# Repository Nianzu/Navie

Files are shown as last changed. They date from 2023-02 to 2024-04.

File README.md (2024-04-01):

# Navie

A little robot that navigates entirely on its own. Hence the name, Navie.

## Implemented Features
* Onboard navigation processing
* Onboard vision processing

## Desired Features
* Extremely low upfront cost (<$100)
* Stereo camera for navigation
* Use brushless motors as drive system
    * FOC on brushless motors
    * Custom motor driver circuit
* Really small (Fit in the palm of the hand)
* Integrated rechargeable battery
* WIFI connectivity



## Technologies
### Depth processing
Depth processing is done using a block-matching algorithm where each pixel is calculated individually, and neighbors are only processed for sub-pixel calculations. In the future, I plan to implement pyramiding and already have the Gaussian resizing function completed.

### Localization
Localization is currently a simple particle filter, with Gaussian noise generated by this function. Currently, there is no past knowledge within each particle, but there are plans to update this in the future.

The algorithm outputs a "best guess" position on the map that the path planner then uses to attempt to route the robot to the goal location.

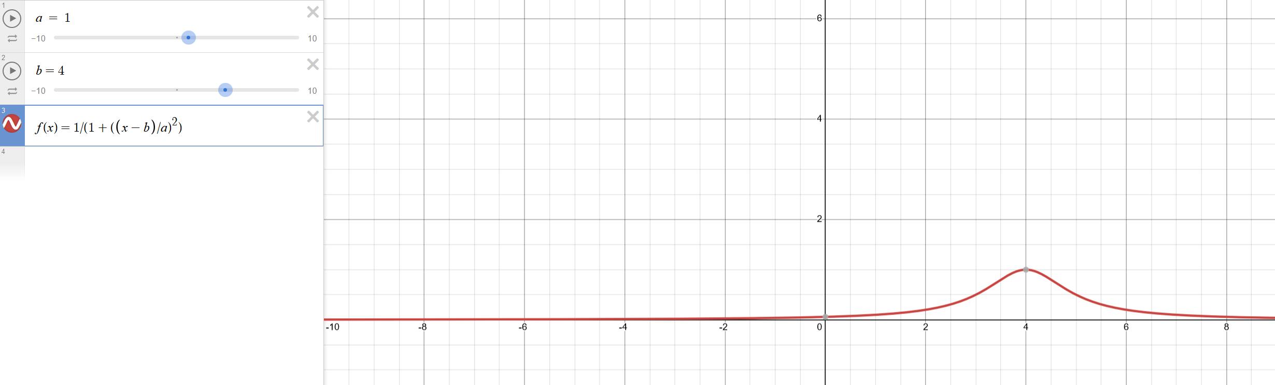
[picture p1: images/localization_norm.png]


### Path planning
The path planning implementation is designed to take a single path with x_1,y_1 start points and x_2,y_2 end points, and recursively split it using an A* approach to generate a valid path. Currently, the path-splitting is buggy so its been removed. Below is a demonstration of the localization and path planning working together to get a robot (white circle with red lines) to the goal position (end of white line) using only the knowledge of the length of the 3 sensors and the map.

You might notice that the green circle/line (the best guess robot) is not correct at first. This is because the map is highly symmetric, so there are lots of valid positions at first

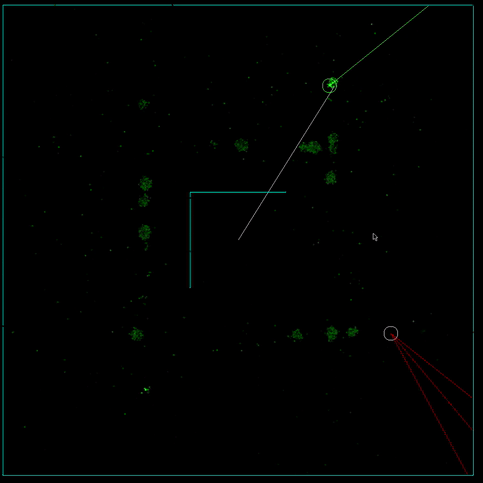
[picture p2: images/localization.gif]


## Hardware
### Processor - Raspberry Pi 4B AND  Raspberry Pi 3 B V1.2
Ideally, this will eventually be a fully custom processor. However, I've been able to benchmark the processing on a Raspberry Pi 4B and it looks like this will be able to run under a second for a full cycle **without any additional optimizations**. Seeing as 1 second was my initial target when I started this project, this is good enough for now. However, due to my choice of camera, I'll have to run 2 pies. The cameras plug into the pi's camera port, and I don't want to pay for a camera multiplexer. So, the plan is for the Pi 4 to transfer the image to the Pi 3, which will run the depth processing. Then the Pi 3 will output sensor vectors to the Pi 4 which will run the particle filter and the motors.

### Cameras - OV5647 x2
Why these cameras? 1: They are cheap. I managed to find a set of 2 of these on amazon for $9. 2: They are high performing, promising 2592 x 1944 still images, 1080p video, and up to 90 fps at 640x480. TODO What more do I need?

<image src="images/OV5647.jpg" width=200>

[Arducam link](https://www.arducam.com/product/arducam-ov5647-standard-raspberry-pi-camera-b0033/)

[Amazon link](https://www.amazon.com/gp/product/B07ZZ2K7WP/ref=ox_sc_act_title_3?smid=A20BQYJRA135IQ&psc=1)

### Motors - N20 knockoff
What do I need in a motor? Encoder feedback, decent build quality, low size and weight. I wanted to get [these](https://www.servocity.com/90-rpm-micro-gear-motor-w-encoder/) from servo city, but I found what looks to be a knockoff on Amazon for half the price. TODO We'll see if I get what I paid for.

<image src="images/motor.jpg" width=200>

[Amazon link](https://www.amazon.com/Reduction-Multiple-Replacement-Velocity-Measurement/dp/B08DKJT2XF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)

### Motor controler - L298N
Cheap, reliable, and most importantly cheap.

<image src="images/motor_driver.jpg" width=200>

[Amazon link](https://www.amazon.com/HiLetgo-Controller-Stepper-H-Bridge-Mega2560/dp/B07BK1QL5T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)

### Power converter - LM2596
### Integration and cooling

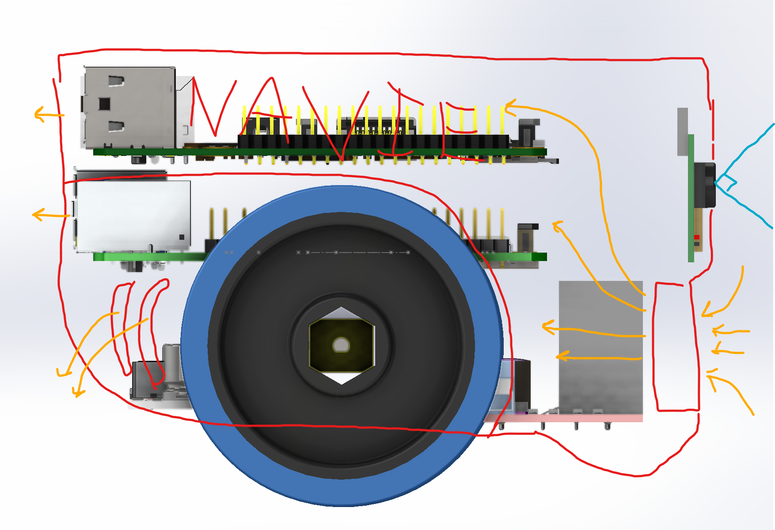
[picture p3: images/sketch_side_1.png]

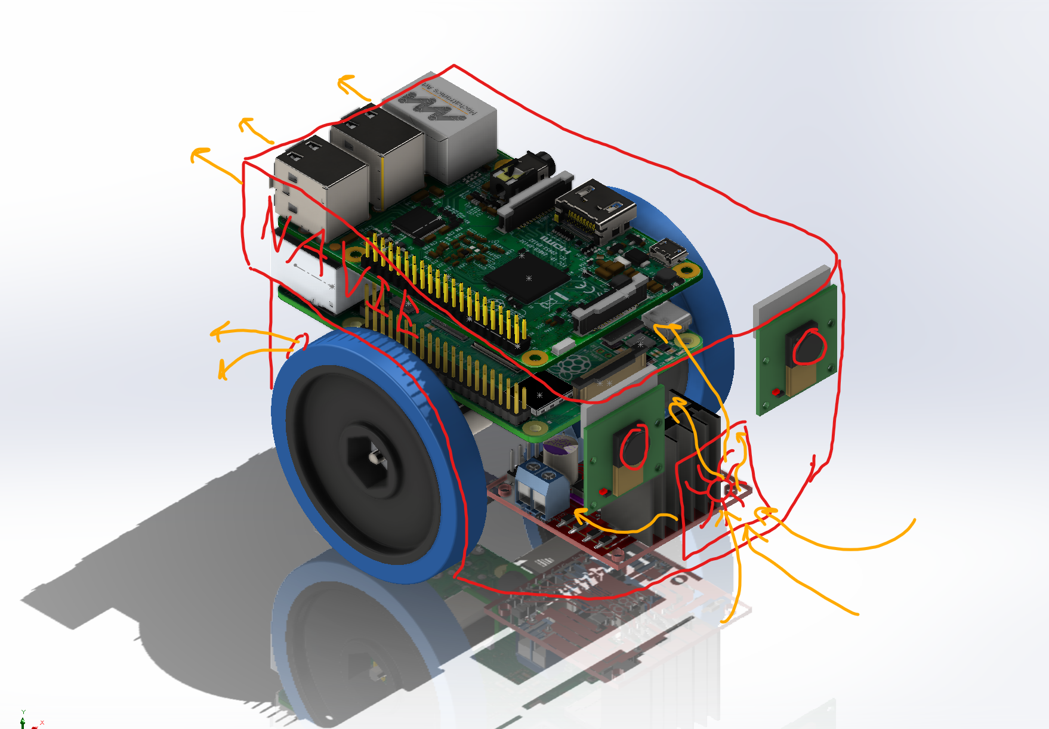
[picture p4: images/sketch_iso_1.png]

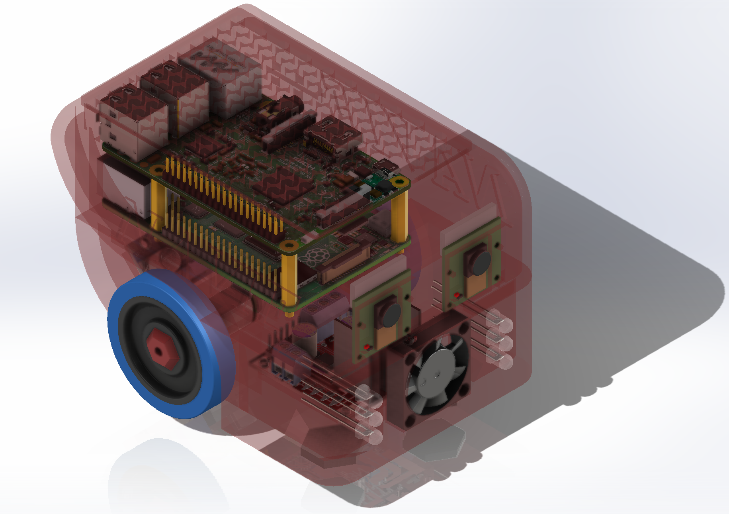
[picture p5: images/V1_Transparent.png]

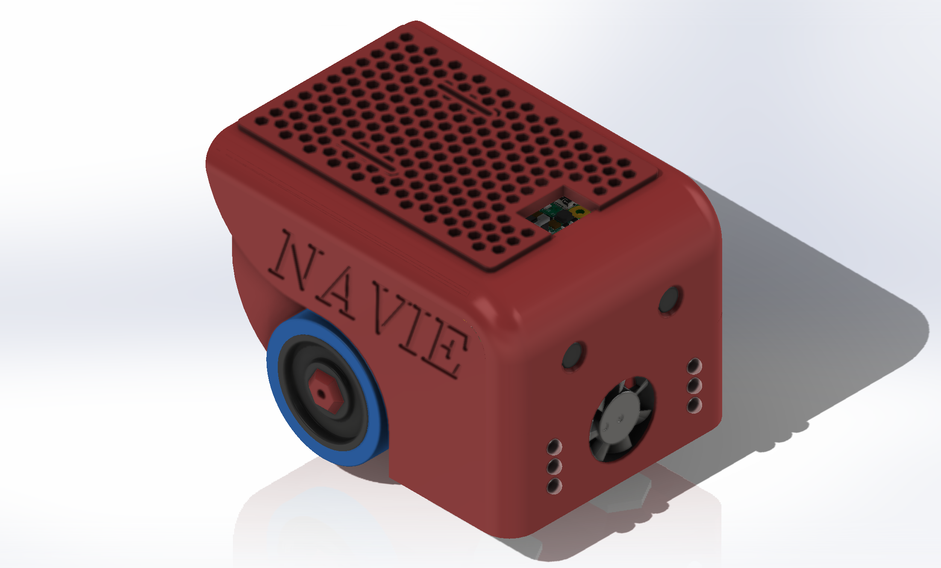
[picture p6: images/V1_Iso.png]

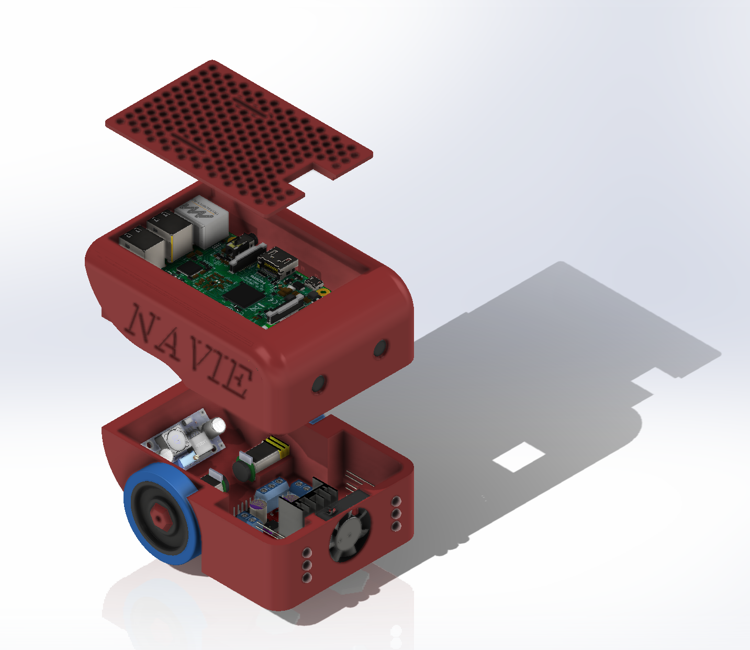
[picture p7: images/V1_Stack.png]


https://banebots.com/banebots-wheel-2-3-8-x-0-4-1-2-hex-mount-50a-black-blue/

## Getting Started
TODO write this section

### Dev environment setup
* Ubuntu running under WSL with VcXsrv for test processes, 
* Non-STL libraries
    * Simple Direct Media Layer (SDL 2) `<SDL2/SDL.h>`. Used to write pixels to the screen. Used due to strong support, ease of use, and cross-platform support.
    ```
    sudo apt install libsdl2-dev
    ```
    * NCurses  `<ncurses.h>`. Used to get key inputs from the user to drive the robot in manual mode.
    ```
    sudo apt install libncurses5-dev libncursesw5-dev
    ```
    * Terminos  `<termios.h>`. Used to set the terminal to non-cannonical mode for easier driving. Seems to come pre-installed with linux, TODO need to check.
    * bcm2835 `<bcm2835.h>`. Used to control the bcm2835 chip on the raspberry pi that handles GPIO. This is our GPIO library.
    ```
    wget http://www.airspayce.com/mikem/bcm2835/bcm2835-1.71.tar.gz
    tar zxvf bcm2835-1.71.tar.gz
    cd bcm2835-1.71
    ./configure
    make
    sudo make check
    sudo make install
    ```

### Compile

#### Depth processing
```
gcc -g main.c -o main.o
```

#### Localization (All subprograms)
```
gcc main.c -o main.o `sdl2-config --cflags --libs` -lm -O3
```

#### Control
```
gcc -o main main.c -lm -lbcm2835
```

#### Test
```
gcc main.c -o main.o
```

## To-Do

### Depth processing
* Confidence rejection
* Filter output image
* Rectify images (not using Middlebury dataset)

### Localization
* Particle filter often finds the wrong node cluster at first.
* Particle filter does not take into account recent history.
* Path planner
* Flood on loss of confidence

### Mechanical
* Consider installing a laser pointer to aid in depth perception of featureless walls. (structured light)
* move zipties back
* Motor driver needs to be filed for fit (too tight)
* Motor driver aleged ineficiencies
* motor driver size
* Wheel hub D shaft is not tight enough. Radius is good, increase length of D-line
* Camera cad is incorrect

## Benchmarks - Depth processing

Execution time for `depth_processing\tsukuba\scene1.row3.col1.ppm` and `depth_processing\tsukuba\scene1.row3.col2.ppm`. All performance is single threaded to make comparisons to future hardware more apt.

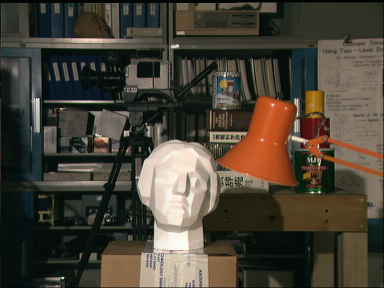
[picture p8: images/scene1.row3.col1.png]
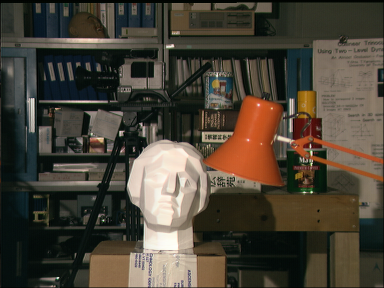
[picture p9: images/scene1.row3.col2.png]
 

### 2/16/2022 Simple block match

```
287/288 - 100%
block_match() took 90.131191 seconds to execute
```
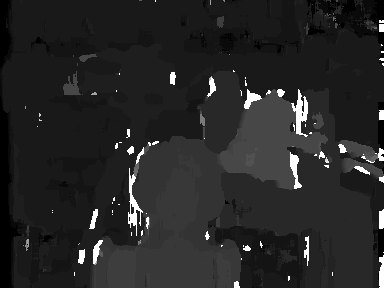
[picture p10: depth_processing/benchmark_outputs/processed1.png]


### 2/17/2022 Full-color block match

```
287/288 - 100%
block_match() took 87.297683 seconds to execute
```
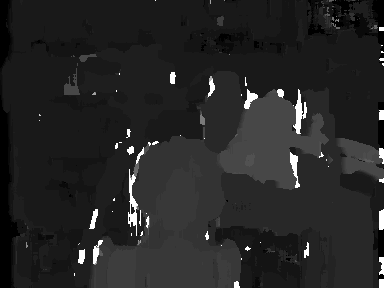
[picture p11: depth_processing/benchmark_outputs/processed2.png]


### 2/17/2022 Fixed block-matching length issue

```
287/288 - 100%
block_match() took 21.699990 seconds to execute
```
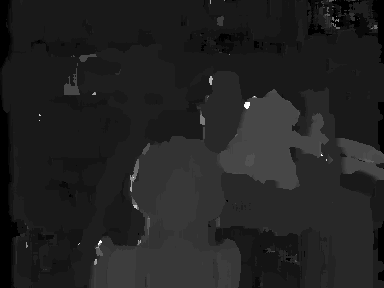
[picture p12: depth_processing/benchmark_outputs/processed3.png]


### 2/17/2022 Sup-pixel disparity

```
287/288 - 100%
block_match() took 21.609720 seconds to execute
```
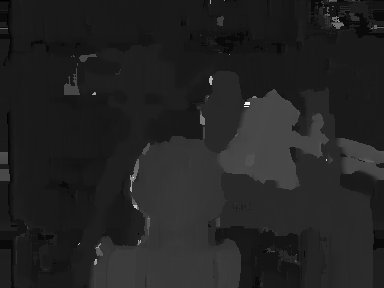
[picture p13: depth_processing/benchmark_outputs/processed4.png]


### 2/17/2022 Search-box optimization + better data structure for depth map

```
287/288 - 100%
block_match() took 3.112148 seconds to execute
```
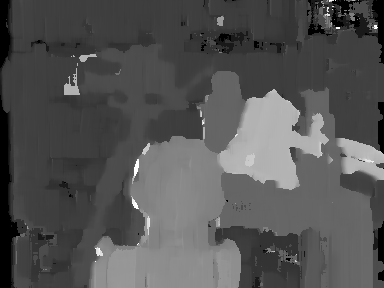
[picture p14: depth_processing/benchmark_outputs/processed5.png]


block_match() took 0.682072 seconds to execute

### 2/20/2022 Added -O3 compiler flag and removed unnecessary prints

```
block_match() took 0.682072 seconds to execute
```


## Benchmarks - Localization

### 2/20/2022 Simple particle filter
T-0
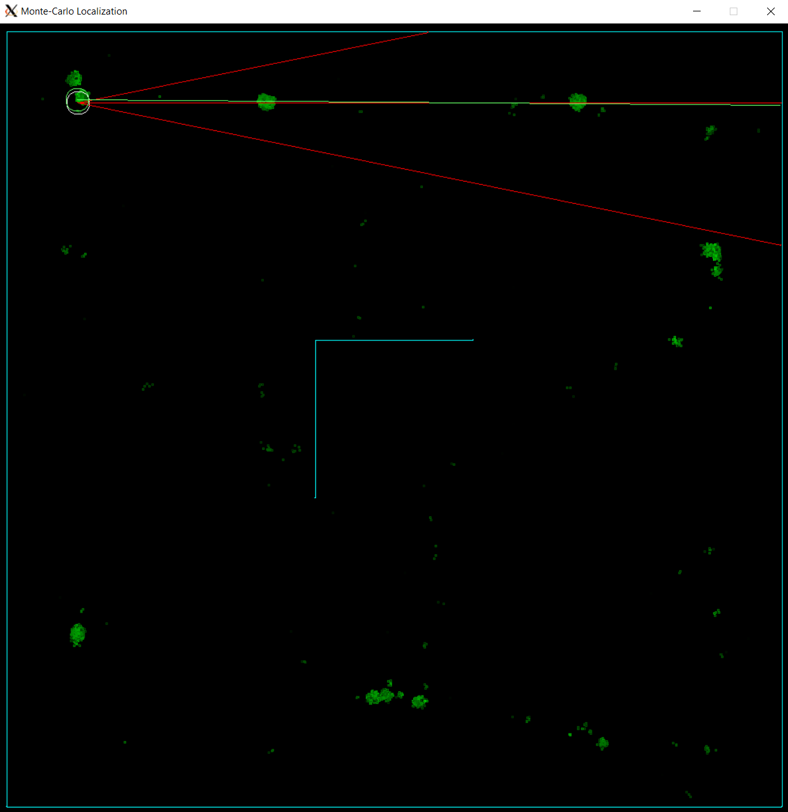
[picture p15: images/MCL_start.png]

T-1
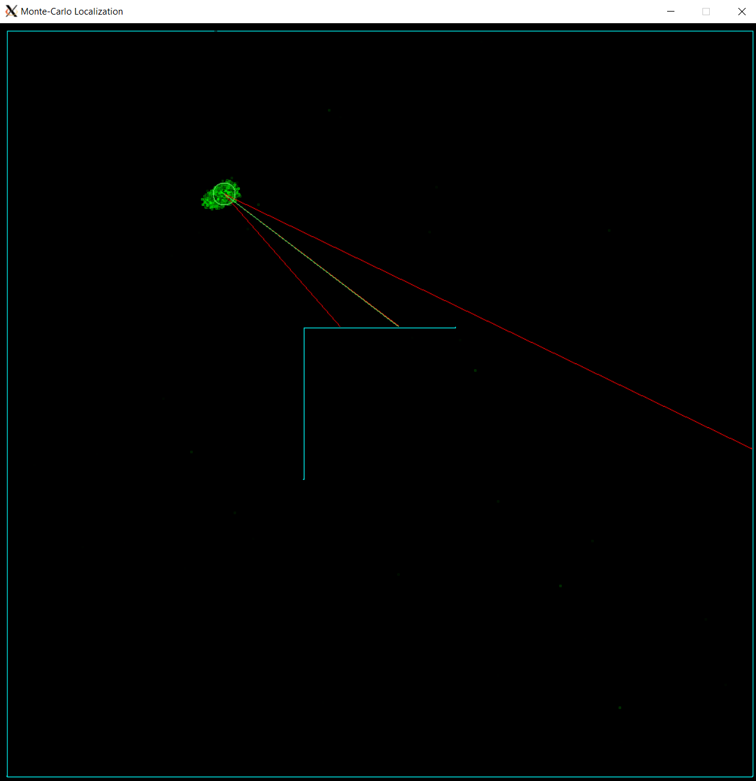
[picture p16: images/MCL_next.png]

```
processing (not including graphics) took 0.027040 seconds to execute.
```
Execution time is ~0.015s per frame, including path planning and particle filtering with 5000 particles.

## Hardware benchmarks

### Raspberry Pi 3 B V1.2
#### Localization
Software Version: 2d94655dcabb89866f78500f899f6fc5ea158938
```
processing (not including graphics) took 0.522824 seconds to execute
```

### Raspberry Pi 4 B
#### Localization
Software Version: 2d94655dcabb89866f78500f899f6fc5ea158938
```
processing (not including graphics) took 0.190935 seconds to execute
```

## Sources
These are the sources that I used to inform my decision on this project, and that I think might be helpful to someone attempting something similar. I've made an effort to provide a general explanation of each source.

### Depth processing
* *Stereo Vision: Depth Estimation between object and camera* - Apar Garg 
    * Generalist beginner explanation of depth processing using block matching, and some of the math behind determining the depth of each pixel.
    * Includes some source code in python
    * https://medium.com/analytics-vidhya/distance-estimation-cf2f2fd709d8

* *Middlebury Stereo Datasets*
    * Great resource for image pairs to test depth processing. Ground truth images are sometimes included.
    * https://vision.middlebury.edu/stereo/data/

* *Depth Estimation: Basics and Intuition* - Daryl Tan
    * Overview of the state of depth processing in CS, including stereo and monocular techniques.
    * Great for understanding the options available for depth processing.
    * https://towardsdatascience.com/depth-estimation-1-basics-and-intuition-86f2c9538cd1

Background (Research paper): https://citeseerx.ist.psu.edu/document?repid=rep1&type=pdf&doi=32aedb3d4e52b879de9a7f28ee0ecee997003271

Background: https://ww2.mathworks.cn/help/visionhdl/ug/stereoscopic-disparity.html

TODO + Source: https://docs.opencv.org/3.4/d3/d14/tutorial_ximgproc_disparity_filtering.html

Dataset: http://sintel.is.tue.mpg.de/depth

Background: https://www.cs.cmu.edu/~16385/s17/Slides/13.2_Stereo_Matching.pdf

Background: http://mccormickml.com/2014/01/10/stereo-vision-tutorial-part-i/

TODO: https://developer.nvidia.com/how-to-cuda-c-cpp

Background: https://dsp.stackexchange.com/questions/75899/appropriate-gaussian-filter-parameters-when-resizing-image

### Localization

Background (Research paper): https://www.ri.cmu.edu/pub_files/pub1/dellaert_frank_1999_2/dellaert_frank_1999_2.pdf

Background + Source: https://fjp.at/posts/localization/mcl/

Background + Source: https://ros-developer.com/2019/04/10/parcticle-filter-explained-with-python-code-from-scratch/

Background (REALLY GOOD): https://www.usna.edu/Users/cs/taylor/courses/si475/notes/slam.pdf

Example: https://www.youtube.com/watch?v=m3L8OfbTXH0

Background (REALLY GOOD):https://www.youtube.com/watch?v=3Yl2aq28LFQ

Background (Research paper): https://research.google.com/pubs/archive/45466.pdf

Background (REALLY GOOD): https://cs.gmu.edu/~kosecka/cs685/cs685-icp.pdf

Background (Research paper): https://arxiv.org/pdf/2007.07627

Background (Research paper): https://www.researchgate.net/figure/Hybrid-algorithm-ideology-ICP-step-by-step-comes-to-local-minima-After-local-minima_fig4_281412803

https://towardsdatascience.com/optimization-techniques-simulated-annealing-d6a4785a1de7
https://resources.mpi-inf.mpg.de/deformableShapeMatching/EG2011_Tutorial/slides/2.1%20Rigid%20ICP.pdf
https://www.visiondummy.com/2014/04/geometric-interpretation-covariance-matrix/
https://www.youtube.com/watch?v=cOUTpqlX-Xs
https://cs.fit.edu/~dmitra/SciComp/Resources/singular-value-decomposition-fast-track-tutorial.pdf
https://iosoft.blog/2020/07/16/raspberry-pi-smi/
https://forums.raspberrypi.com/viewtopic.php?t=228727
https://raspberrypi.stackexchange.com/questions/130529/how-fast-are-c-python-libraries
https://forums.raspberrypi.com/viewtopic.php?t=244031
PERIPHERAL BASE ADDRESS FOR RASPBERRY PI 4 is  0xFE000000
https://raspberrypi.stackexchange.com/questions/124985/using-motor-encoders-with-raspberry-pi
### Camera processing
Background: https://www.raspberrypi.com/documentation/computers/camera_software.html#getting-started

Source: https://stackoverflow.com/questions/41440245/reading-camera-image-using-raspistill-from-c-program

Server Stream: libcamera-vid -t 0 --inline --listen -o tcp://0.0.0.0:8000
Server Stream 60fps: libcamera-vid -t 0 --inline --listen -o tcp://0.0.0.0:8000 --level 4.2 --framerate 120 --width 1280 --height 720 --denoise cdn_off

Client: ffplay tcp://10.0.0.73:8000 -vf "setpts=N/30" -fflags nobuffer -flags low_delay -framedrop
ffplay tcp://10.0.0.73:8000 -vf "hflip,vflip" -flags low_delay -framedrop

## Contributions

Contributions are always welcome. If you want to contribute to the project, please create a pull request.

## License

This project is not currently licensed, but I will look into adding a license at a later date.

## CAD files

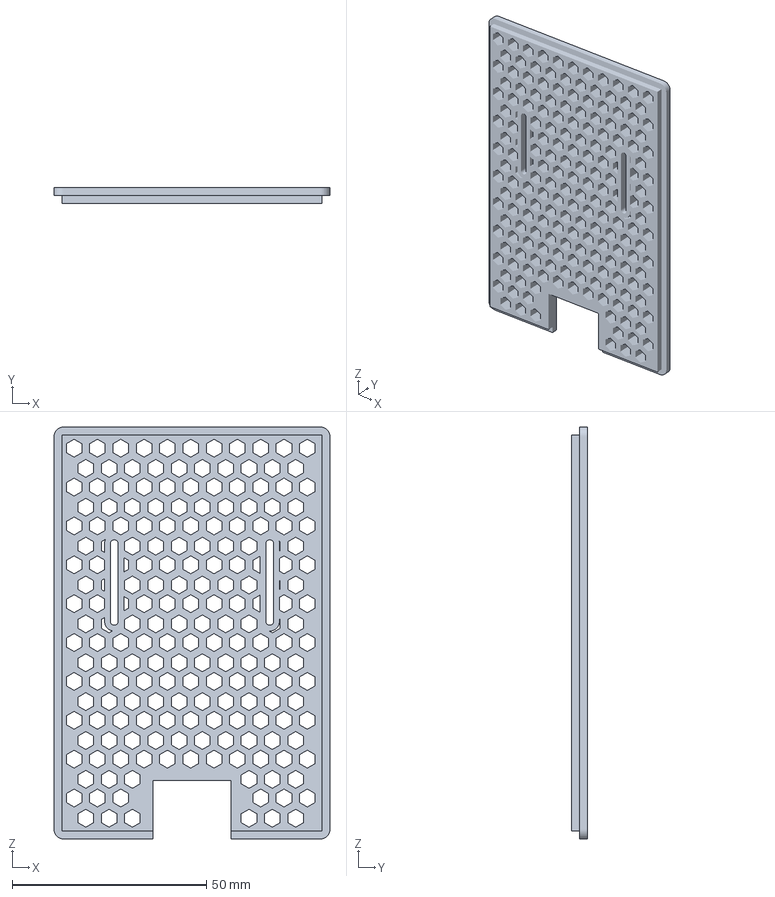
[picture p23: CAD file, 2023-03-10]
hardware/3D prints/lid.3MF
71.0 x 4.00 x 106.0 mm

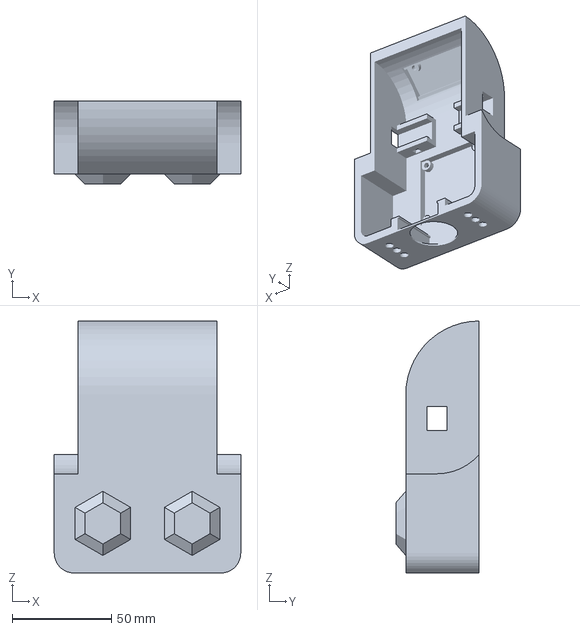
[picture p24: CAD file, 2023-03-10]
hardware/3D prints/base_frame.3MF
94.0 x 42.0 x 127.0 mm

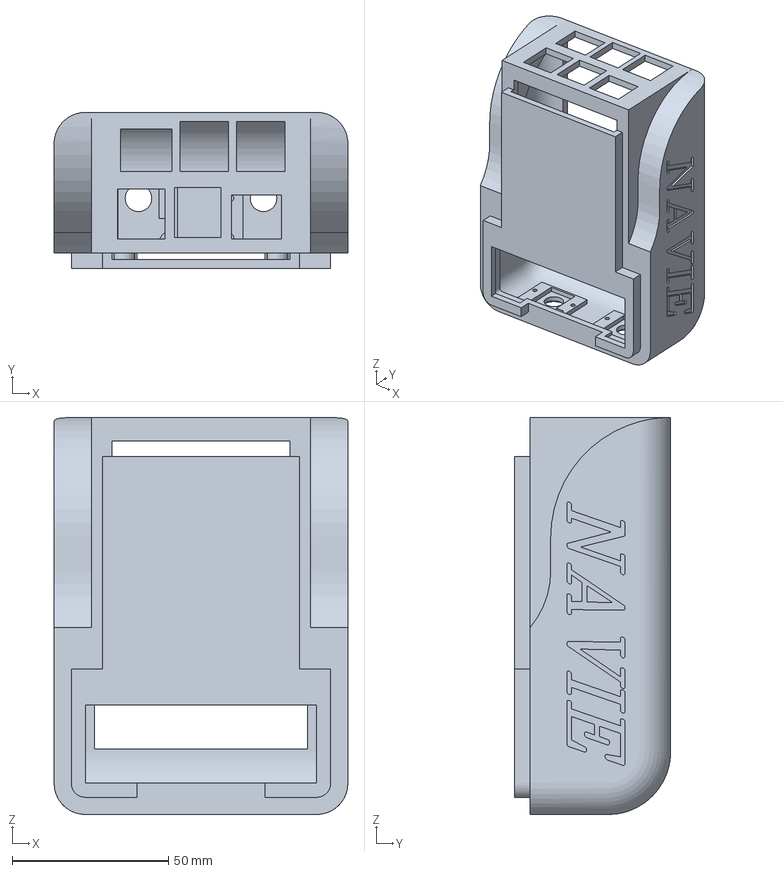
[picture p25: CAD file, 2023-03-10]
hardware/3D prints/top_frame.3MF
94.0 x 50.0 x 127.0 mm

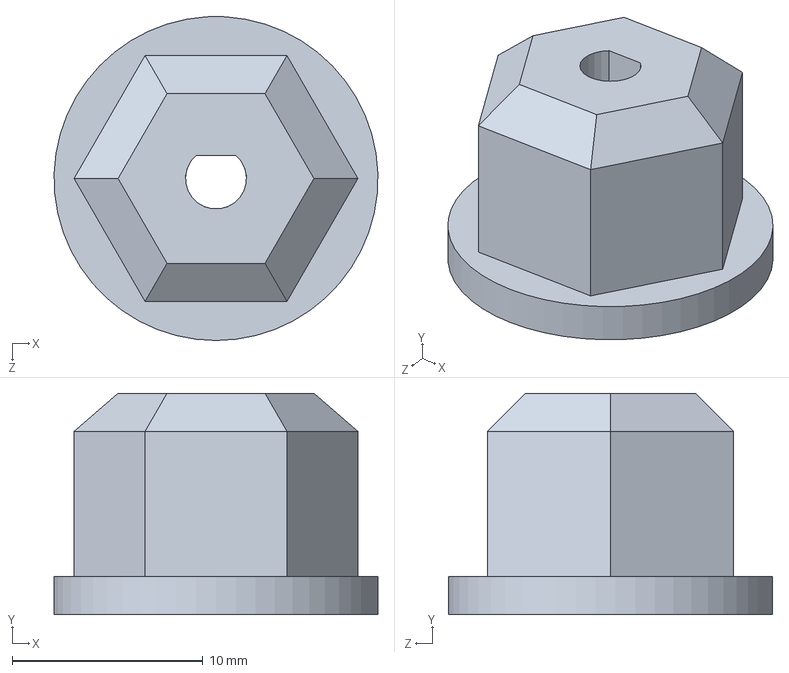
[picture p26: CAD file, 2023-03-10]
hardware/custom/hex_hub_1-2_in.SLDPRT
17.0 x 11.6 x 17.0 mm

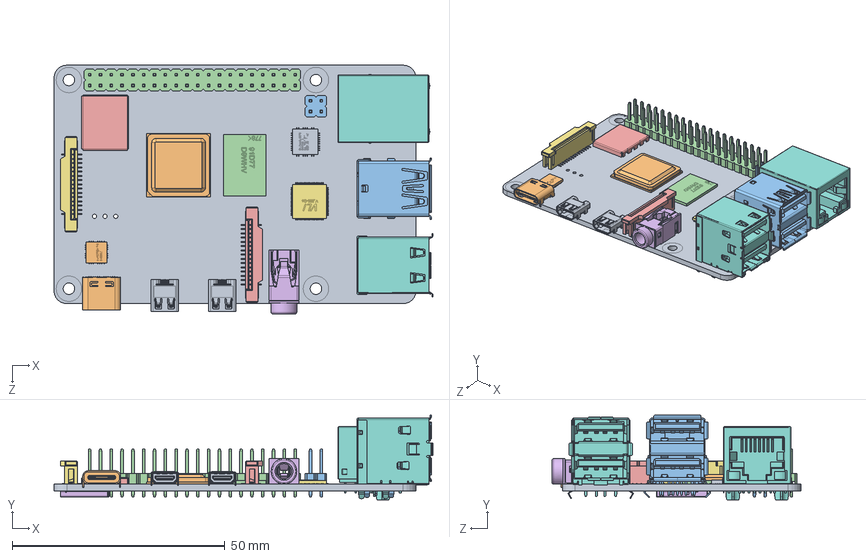
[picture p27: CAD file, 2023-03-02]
hardware/cots/raspberry-pi-4-model-b-1.snapshot.3/Raspberry Pi 4 Model B.SLDASM
89.0 x 19.9 x 58.4 mm
PCB, RPi4ModelB
Broadcom BCM2711B0 CPU, RPi4ModelB
2.54 mm DUPONT MALE PIN HEADER, POE, 2X2, RPi4ModelB
2.54 mm DUPONT MALE PIN HEADER, IO, 2X20, RPi4ModelB
Camera Connector, RPi4ModelB
Microphone Plug, RPi4ModelB
Display Connector, RPi4ModelB
Gigabit Ethernet Port, RPi4ModelB
Female Micro HDMI Connector, RPi4ModelB x 2
Female USB Type C Connector, RPi4ModelB
2X USB3.0 PORTS, RPi4ModelB
91D77 D9WHV 778K, 4 GB LPDDR4 SDRAM, RPi4ModelB
Cypress CYW43455 Wireless Module Cover, RPi4ModelB
SD Card Slot, RPi4ModelB
VIA VL805 PCIe USB 3.0 controller, RPi4ModelB
2X USB2.0 PORTS, RPi4ModelB
Broadcom BCM54213PE Gigabit Ethernet Transceiver, RPi4ModelB
MxL7704 Universal PMIC, RPi4ModelB

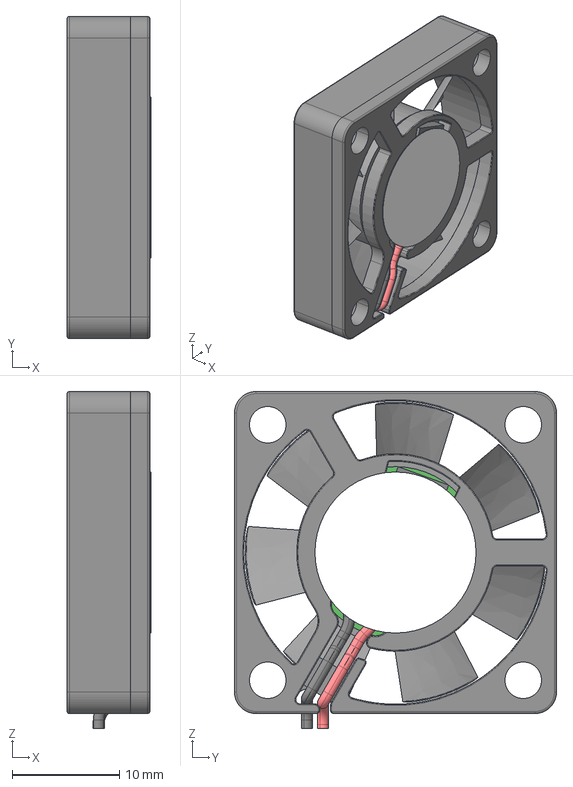
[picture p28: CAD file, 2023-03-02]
hardware/cots/fan-30x30x8-dc5v-guncaizhu-1.snapshot.1/GUNCAIZHU_Fan DC brushless_30x30x8_5V_(no text).stp
7.80 x 30.0 x 31.4 mm

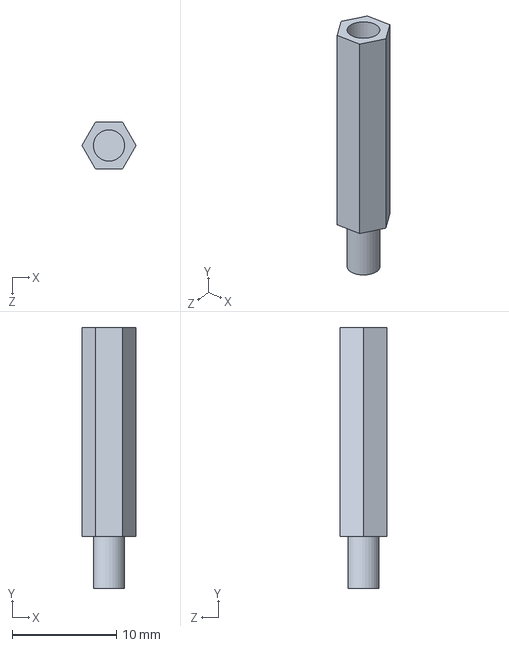
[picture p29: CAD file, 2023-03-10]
hardware/cots/hex_standoff_20mm.SLDPRT
5.20 x 25.0 x 4.50 mm

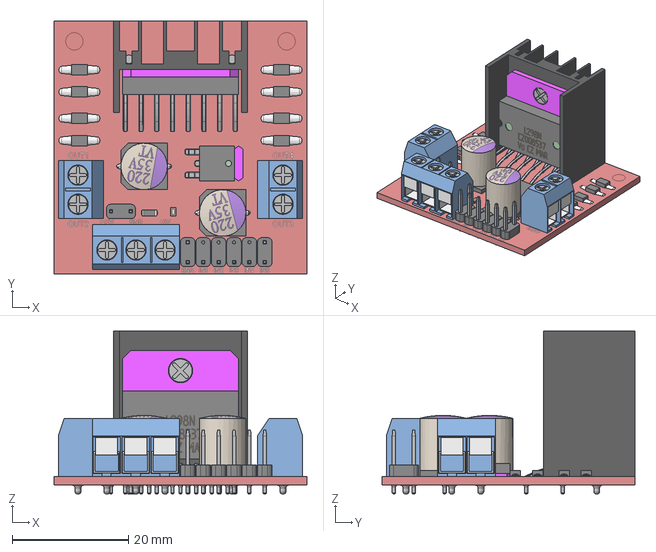
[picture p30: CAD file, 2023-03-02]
hardware/cots/l298n-17.snapshot.2/L298N.stp
43.5 x 43.5 x 28.0 mm

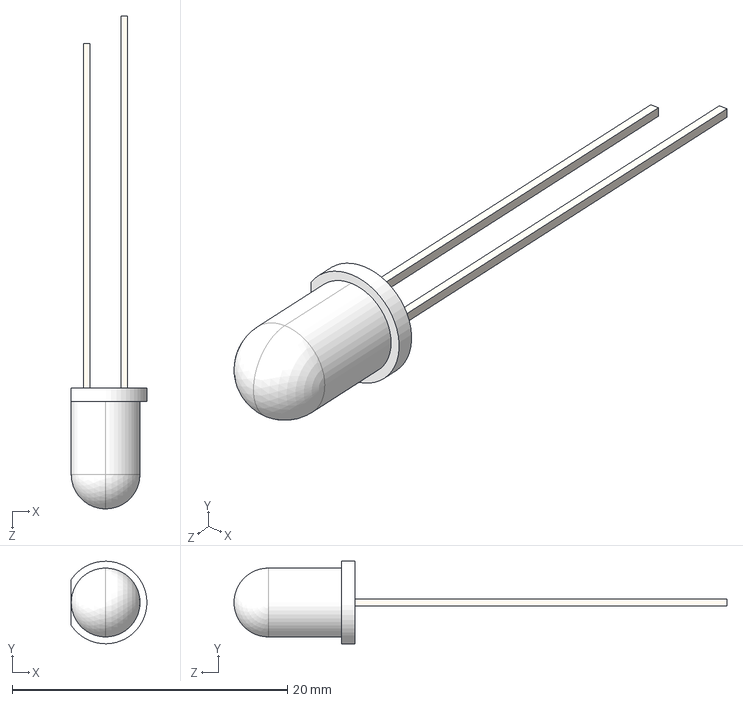
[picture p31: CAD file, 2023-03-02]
hardware/cots/led-5mm-1.snapshot.6/LED 5mm.STEP
5.49 x 6.00 x 35.8 mm

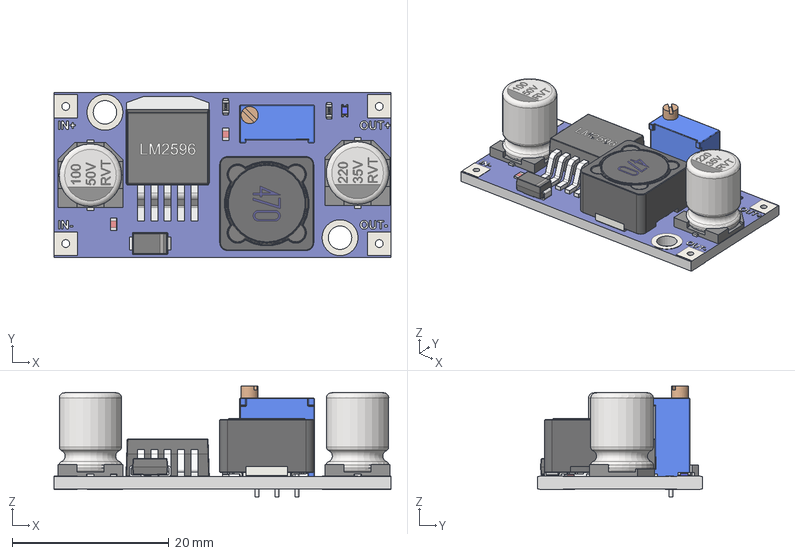
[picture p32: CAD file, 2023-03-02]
hardware/cots/lm2596-dc-dc-stepdown-converter-1.snapshot.2/LM2596 DC-DC StepDown Converter v1.step
43.0 x 21.0 x 14.2 mm
Board v5
Trimpot 3296W v1
CDRH127_470M v1
CAPSMD220-35 v1
CAPSMD100-50 v1
TO-263BA v2
DO-214AC-DIOM5127X23N v1
Resistor 0603 v1
Resistor 0603 v1 (1)
CAP0603 v1
LED Blue SMD 0603 Würth 150060BS55040 v1
CAP0603 v1 (1)

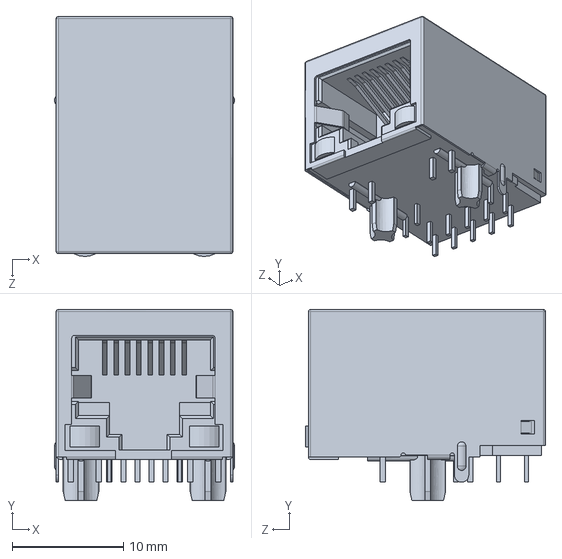
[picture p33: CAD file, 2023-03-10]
hardware/cots/raspberry-pi-4-model-b-1.snapshot.3/Gigabit Ethernet Port, RPi4ModelB.SLDPRT
16.2 x 17.2 x 21.6 mm

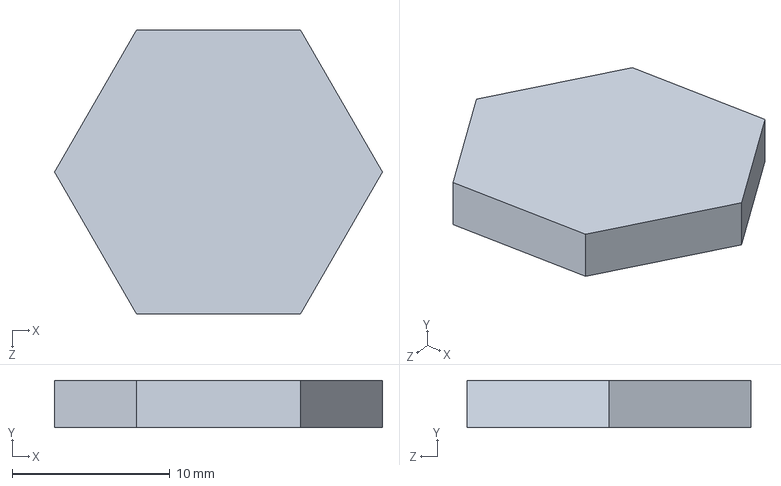
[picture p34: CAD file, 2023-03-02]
hardware/cots/led-5mm-1.snapshot.6/felt_hex_pad.SLDPRT
20.8 x 3.00 x 18.0 mm

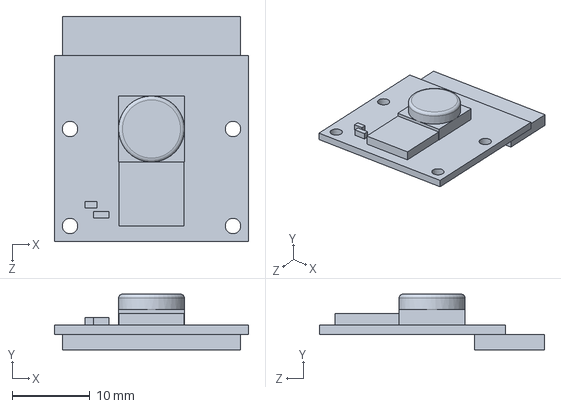
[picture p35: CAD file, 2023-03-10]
hardware/cots/OV5647_B0033.SLDPRT
25.0 x 7.20 x 29.0 mm

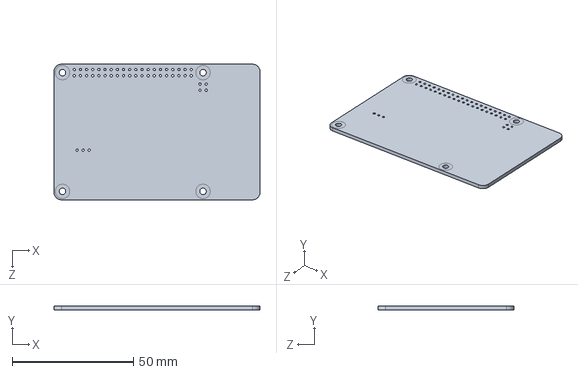
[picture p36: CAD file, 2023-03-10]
hardware/cots/raspberry-pi-4-model-b-1.snapshot.3/PCB, RPi4ModelB.SLDPRT
85.0 x 1.60 x 56.0 mm

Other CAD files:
hardware/custom/lid.SLDPRT
hardware/custom/base_frame.SLDPRT
hardware/3D prints/hex_hub_1-2_in.3MF
hardware/custom/top_frame.SLDPRT
hardware/cots/BaneBots_Wheel_1_78.SLDPRT
hardware/cots/BaneBots_Wheel_T40P-245BA-HS4.SLDPRT
hardware/cots/N20_Gear_Motor.SLDPRT
hardware/cots/led-5mm-1.snapshot.6/LED 5mm.IGS
hardware/cots/led-5mm-1.snapshot.6/LED 5mm.SLDPRT
hardware/cots/led-5mm-1.snapshot.6/LED 5mm.STL
hardware/cots/lm2596-dc-dc-stepdown-converter-1.snapshot.2/LM2596 DC-DC StepDown Converter v1.f3d
hardware/cots/raspberry-pi-4-model-b-1.snapshot.3/2.54 mm DUPONT MALE PIN HEADER, IO, 2X20, RPi4ModelB.SLDPRT
hardware/cots/raspberry-pi-4-model-b-1.snapshot.3/2.54 mm DUPONT MALE PIN HEADER, POE, 2X2, RPi4ModelB.SLDPRT
hardware/cots/raspberry-pi-4-model-b-1.snapshot.3/2X USB2.0 PORTS, RPi4ModelB.SLDPRT
hardware/cots/raspberry-pi-4-model-b-1.snapshot.3/2X USB3.0 PORTS, RPi4ModelB.SLDPRT
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

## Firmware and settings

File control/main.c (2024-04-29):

// g++ -o test main.c Realtime.cc -lm -lpigpio

#include <pigpio.h>
#include <stdio.h>
#include <unistd.h>
#include <termios.h>
#include <signal.h>
#include <stdlib.h>
#include <fcntl.h>
#include <math.h>

// Define GPIO pins according to Broadcom numbering
#define MOTOR_L_R 25 // GPIO25, equivalent to physical pin 22
#define MOTOR_L_F 8  // GPIO8, equivalent to physical pin 24
#define MOTOR_R_F 7  // GPIO7, equivalent to physical pin 26
#define MOTOR_R_R 24 // GPIO24, equivalent to physical pin 18

#define LIGHT_L 2 // GPIO2, equivalent to physical pin 3
#define LIGHT_R 3 // GPIO3, equivalent to physical pin 5

#define ENCODER_L_A 10 // GPIO10, equivalent to physical pin 19
#define ENCODER_L_B 9  // GPIO9, equivalent to physical pin 21
#define ENCODER_R_A 17 // GPIO17, equivalent to physical pin 11
#define ENCODER_R_B 27 // GPIO27, equivalent to physical pin 13

#define TICKS_PER_REV 3575.0855
#define TICKS_PER_RAD 568.99252930116018242497
#define WHEEL_CIRCUMFERENCE 0.147
#define MAX_SPEED 255

struct termios orig_term;

void restore_terminal()
{
    // Restore the original terminal settings
    tcsetattr(STDIN_FILENO, TCSANOW, &orig_term);
}

void setup_terminal() {
    struct termios term;
    tcgetattr(STDIN_FILENO, &term);
    orig_term = term;
    // term.c_lflag &= ~(ICANON | ECHO);
    term.c_lflag &= ~(ICANON);
    tcsetattr(STDIN_FILENO, TCSANOW, &term);
}

char read_keyboard_input()
{
    char c;
    read(STDIN_FILENO, &c, 1);
    return c;
}

#define STATE_MASK 0x03 // Mask to extract the last two bits (encoder states)
#define CW 1            // Clockwise rotation identifier
#define CCW -1          // Counter-clockwise rotation identifier

int8_t state_table[] = {
    0, // 00 to 00: No change
    CW, // 00 to 01: Clockwise step
    CCW, // 00 to 10: Counter-clockwise step
    0, // 00 to 11: Invalid transition
    CCW, // 01 to 00: Counter-clockwise step
    0, // 01 to 01: No change
    -2, // 01 to 10: Invalid transition
    CW, // 01 to 11: Clockwise step
    CW, // 10 to 00: Clockwise step
    2, // 10 to 01: Invalid transition
    0, // 10 to 10: No change
    CCW, // 10 to 11: Counter-clockwise step
    0, // 11 to 00: Invalid transition
    CCW, // 11 to 01: Counter-clockwise step
    CW, // 11 to 10: Clockwise step
    0 // 11 to 11: No change
};

int update_encoder(uint8_t *encoder_l_a, uint8_t *encoder_l_b, uint8_t encoder_l_a_new, uint8_t encoder_l_b_new) {
    uint8_t old_state = (*encoder_l_a << 1) | *encoder_l_b;
    uint8_t new_state = (encoder_l_a_new << 1) | encoder_l_b_new;
    int output = state_table[(old_state << 2) | new_state]; // Shift old state 2 bits left and add new state
    // if (output >1)
    // {
    //     printf("ERROR %d\n",output);
    // }
    *encoder_l_a = encoder_l_a_new;
    *encoder_l_b = encoder_l_b_new;

    return output;
}

enum motion {
  fwd,
  rev,
  stop
}; 

enum motors {
    left,
    right
};

void set_motor(motors motor_sel, motion motion_sel, int speed)
{
    gpioPWM(motor_sel == left ? 12 : 13, speed);
    switch (motion_sel)
    {
        case fwd:
            gpioWrite(motor_sel == left ? MOTOR_L_F : MOTOR_R_F, PI_HIGH);
            gpioWrite(motor_sel == left ? MOTOR_L_R : MOTOR_R_R, PI_LOW);
            break;
        case rev:
            gpioWrite(motor_sel == left ? MOTOR_L_F : MOTOR_R_F, PI_LOW);
            gpioWrite(motor_sel == left ? MOTOR_L_R : MOTOR_R_R, PI_HIGH);
            break;
        default:
        case stop:
            gpioWrite(motor_sel == left ? MOTOR_L_F : MOTOR_R_F, PI_LOW);
            gpioWrite(motor_sel == left ? MOTOR_L_R : MOTOR_R_R, PI_LOW);
            break;
    }
}

typedef struct {
    double Kp;
    double Ki;
    double Kd;
    int last_error;
    double integral;
} PIDController;

void PID_Init(PIDController* pid, double Kp, double Ki, double Kd) {
    pid->Kp = Kp;
    pid->Ki = Ki;
    pid->Kd = Kd;
    pid->last_error = 0;
    pid->integral = 0.0;
}

int PID_Update(PIDController* pid, int setpoint, int actual) {
    int error = setpoint - actual;
    pid->integral += error;
    double derivative = error - pid->last_error;
    int output = (int)(pid->Kp * error + pid->Ki * pid->integral + pid->Kd * derivative);
    pid->last_error = error;
    return output;
}

void drive_distance_in_time(double distance_meters, double total_time_seconds, bool flip_left) {
    double ticks_per_meter = TICKS_PER_REV / WHEEL_CIRCUMFERENCE;
    int total_ticks = (int)(distance_meters * ticks_per_meter);

    // Time allocation (in seconds, for clarity)
    double accel_time = total_time_seconds / 3;
    double decel_time = accel_time; 
    double constant_speed_time = total_time_seconds - 2 * accel_time;
    
    // Speed calculations (in ticks per second for simplicity)
    int max_speed_ticks_per_second = total_ticks / (accel_time + constant_speed_time);
    
    PIDController pid_left, pid_right;
    PID_Init(&pid_left, 1, 0.000001, 0.01);
    PID_Init(&pid_right, 1, 0.000001, 0.01);
    // PID_Init(&pid_left, 0.1, 0.00, 0.05);
    // PID_Init(&pid_right, 0.1, 0.00, 0.05);

    struct timespec start, current;
    clock_gettime(CLOCK_MONOTONIC, &start);
    long long current_time_ns = 0;
    double current_time_seconds = 0;
    int current_left_ticks = 0, current_right_ticks = 0;
    int target_ticks = 0;

    uint8_t encoder_l_a = gpioRead(ENCODER_L_A);
    uint8_t encoder_l_b = gpioRead(ENCODER_L_B);
    uint8_t encoder_r_a = gpioRead(ENCODER_R_A);
    uint8_t encoder_r_b = gpioRead(ENCODER_R_B);
    double right_scale = 1.5;

    while (abs(current_left_ticks - (flip_left ? -total_ticks : total_ticks)) > abs(total_ticks / 40) || abs(current_right_ticks/right_scale - total_ticks) > abs(total_ticks / 40)) {
        clock_gettime(CLOCK_MONOTONIC, &current);
        current_time_ns = (current.tv_sec - start.tv_sec) * 1000000000LL + (current.tv_nsec - start.tv_nsec);
        current_time_seconds = current_time_ns / 1e9; // Convert nanoseconds to seconds for calculations

        // Calculate target_ticks based on trapezoidal profile
        if (current_time_seconds <= accel_time) 
        {
            target_ticks = (max_speed_ticks_per_second * current_time_seconds / accel_time) * current_time_seconds / 2;
        } else if (current_time_seconds <= (accel_time + constant_speed_time)) {
            target_ticks = max_speed_ticks_per_second * (current_time_seconds - accel_time / 2);
        } else if (current_time_seconds < total_time_seconds) {
            double t_dec = current_time_seconds - accel_time - constant_speed_time;
            target_ticks = (max_speed_ticks_per_second * (accel_time + constant_speed_time / 2)) + max_speed_ticks_per_second * t_dec - (max_speed_ticks_per_second * t_dec / decel_time) * t_dec / 2;
        } else {
            target_ticks = total_ticks;
        }

        // printf("%f %d %d %d\n",current_time_seconds,target_ticks,current_left_ticks,current_right_ticks);

        // Update PID controllers for each motor
        int left_speed = PID_Update(&pid_left, flip_left ? -target_ticks : target_ticks, current_left_ticks);
        int right_speed = PID_Update(&pid_right, target_ticks, current_right_ticks/right_scale);

        // Clamp speeds to [-MAX_SPEED, MAX_SPEED]
        left_speed = fmax(-MAX_SPEED, fmin(left_speed, MAX_SPEED));
        right_speed = fmax(-MAX_SPEED, fmin(right_speed, MAX_SPEED));
        // printf("\t%d\n",left_speed);
        set_motor(left, left_speed > 0 ? fwd : rev, abs(left_speed));
        set_motor(right, right_speed > 0 ? fwd : rev, abs(right_speed));

        // Update current encoder counts
        uint8_t encoder_l_a_new = gpioRead(ENCODER_L_A);
        uint8_t encoder_l_b_new = gpioRead(ENCODER_L_B);
        uint8_t encoder_r_a_new = gpioRead(ENCODER_R_A);
        uint8_t encoder_r_b_new = gpioRead(ENCODER_R_B);
        current_left_ticks -= update_encoder(&encoder_l_a, &encoder_l_b, encoder_l_a_new, encoder_l_b_new);
        current_right_ticks += update_encoder(&encoder_r_a, &encoder_r_b, encoder_r_a_new, encoder_r_b_new);
    }

    // Stop motors after reaching the target
    set_motor(left, stop, 0);
    set_motor(right, stop, 0);
}

void turn_right()
{
    drive_distance_in_time(-0.043,2,true);
}

void turn_left()
{
    drive_distance_in_time(0.043,2,true);
}

int main(int argc, char **argv)
{
    // Set the terminal to take inputs immediately, without waiting for [ENTER]
    setup_terminal();
    if (gpioInitialise() < 0)
        return 1;

    int flags = fcntl(STDIN_FILENO, F_GETFL, 0);
    fcntl(STDIN_FILENO, F_SETFL, flags | O_NONBLOCK);

    // Configure the two PWM ports that control the speed of the wheels
    // Left
    gpioSetMode(12,PI_ALT0);
    gpioSetPWMfrequency(12, 1000); // PWM0

    // Right
    gpioSetMode(13,PI_ALT0);
    gpioSetPWMfrequency(13, 1000); // PWM0

    // Set the motors as outputs
    gpioSetMode(MOTOR_L_R, PI_OUTPUT);
    gpioSetMode(MOTOR_L_F, PI_OUTPUT);
    gpioSetMode(MOTOR_R_F, PI_OUTPUT);
    gpioSetMode(MOTOR_R_R, PI_OUTPUT);

    // Set the lights as outputs
    gpioSetMode(LIGHT_L, PI_OUTPUT);
    gpioSetMode(LIGHT_R, PI_OUTPUT);

    gpioWrite(LIGHT_L, PI_LOW);
    gpioWrite(LIGHT_R, PI_LOW);

    // Set the encoders as inputs
    gpioSetMode(ENCODER_L_A, PI_INPUT);
    gpioSetMode(ENCODER_L_B, PI_INPUT);
    
    // Init the encoders
    uint8_t encoder_l_a = gpioRead(ENCODER_L_A);
    uint8_t encoder_l_b = gpioRead(ENCODER_L_B);
    uint8_t encoder_r_a = gpioRead(ENCODER_R_A);
    uint8_t encoder_r_b = gpioRead(ENCODER_R_B);


    int c;
    int num_ticks = 0;
    while (1)
    {
        c = read_keyboard_input();
        if (c == 'w')
        {
            // Move the robot forward
            printf("For\n");
            set_motor(right, fwd, 255);
            set_motor(left, fwd, 255);
        }
        else if (c == 'a')
        {
            // Turn the robot left
            printf("L\n");
            set_motor(right, fwd, 100);
            set_motor(left, rev, 100);
        }
        else if (c == 's')
        {
            // Move the robot backward
            printf("Rev\n");
            set_motor(right, rev, 255);
            set_motor(left, rev, 255);
        }
        else if (c == 'd')
        {
            // Turn the robot right
            printf("R\n");
            set_motor(right, rev, 100);
            set_motor(left, fwd, 100);
        }
        else if (c == ' ')
        {
            // Stop the robot
            printf("STOP\n");
            set_motor(right, stop, 0);
            set_motor(left, stop, 0);
        }
        else if (c == 'p')
        {
            // Print some information
            printf("%d\n",num_ticks);
        }
        else if (c == 'k')
        {
            drive_distance_in_time(0.4,10,false);
        }
        else if (c == 'm')
        {
            drive_distance_in_time(-0.4,10,false);
        }
        else if (c == 'l')
        {
            turn_right();
        }
        else if (c == 'j')
        {
            turn_left();
        }
        else if (c == 'r')
        {
            drive_distance_in_time(0.2,5,false);
            turn_left();
            drive_distance_in_time(0.2,5,false);
            turn_left();
            drive_distance_in_time(0.2,5,false);
	    turn_right();
            drive_distance_in_time(0.6,12,false);
	    turn_right();
            drive_distance_in_time(0.4,8,false);
	    turn_right();
            drive_distance_in_time(0.2,5,false);
        }
        else if (c == 'e')
        {
            break;
        }

        // CW is positive ticks
        uint8_t encoder_l_a_new = gpioRead(ENCODER_L_A);
        uint8_t encoder_l_b_new = gpioRead(ENCODER_L_B);
        uint8_t encoder_r_a_new = gpioRead(ENCODER_R_A);
        uint8_t encoder_r_b_new = gpioRead(ENCODER_R_B);
        // left encoder update
        // num_ticks += update_encoder(&encoder_l_a, &encoder_l_b, encoder_l_a_new, encoder_l_b_new);
        num_ticks += update_encoder(&encoder_r_a, &encoder_r_b, encoder_r_a_new, encoder_r_b_new);
    }
    restore_terminal();
    gpioTerminate();
    return 0;
}

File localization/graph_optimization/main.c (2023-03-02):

// Nico Zucca, 1/2023

// Compile cmd:
// export LD_LIBRARY_PATH="/usr/local/lib"
// gcc main.c -o main.o `sdl2-config --cflags --libs` -lm -O3

#include <SDL2/SDL.h>
#include <math.h>
#include <limits.h>
#include <time.h>

// Height of the window
#define WINDOW_WIDTH 1000
// Width of the window
#define WINDOW_HEIGHT 1000
// Sensor offset for the side sensors in radians
#define SENSOR_OFFSET 0.75 //~90 deg
// Number of new nodes to create per second
#define MAX_NODE_FREQUENCY 1
// Number of sensors total
#define NUM_SENSORS 100

// Sensor vector
typedef struct sensor_vector
{
    double angle; // Rotation in radians
    double length;
    struct sensor_vector *next;
} sensor_vector;

// Agent object.
typedef struct agent
{
    double x;
    double y;
    double angle; // Rotation in radians
    struct sensor_vector *measurements;
} agent;

// Used to store anticipated movement
typedef struct movement
{
    double x;
    double y;
    double angular;

    double linear_total;
    double angular_total;
} movement;

// Path object
typedef struct connection
{
    double h;
    double x_1;
    double y_1;
    double x_2;
    double y_2;
    struct connection *next;
} connection;

// Graph node object
typedef struct graph_node
{
    // Connections
    double x, y, angular; // relative offset from last position
    double strength;      // 0-1

    // Error
    double err_x, err_y, err_a; // Anticipated max error in each x, y, a from last coordinate

    // Measurements
    struct sensor_vector *measurements;

    // Next chronological node
    struct graph_node *next;

} graph_node;

// Draw a circle on the screen
// Source: https://stackoverflow.com/questions/38334081/how-to-draw-circles-arcs-and-vector-graphics-in-sdl
void DrawCircle(SDL_Renderer *renderer, int32_t centreX, int32_t centreY, int32_t radius)
{
    const int32_t diameter = (radius * 2);

    int32_t x = (radius - 1);
    int32_t y = 0;
    int32_t tx = 1;
    int32_t ty = 1;
    int32_t error = (tx - diameter);

    while (x >= y)
    {
        //  Each of the following renders an octant of the circle
        SDL_RenderDrawPoint(renderer, centreX + x, centreY - y);
        SDL_RenderDrawPoint(renderer, centreX + x, centreY + y);
        SDL_RenderDrawPoint(renderer, centreX - x, centreY - y);
        SDL_RenderDrawPoint(renderer, centreX - x, centreY + y);
        SDL_RenderDrawPoint(renderer, centreX + y, centreY - x);
        SDL_RenderDrawPoint(renderer, centreX + y, centreY + x);
        SDL_RenderDrawPoint(renderer, centreX - y, centreY - x);
        SDL_RenderDrawPoint(renderer, centreX - y, centreY + x);

        if (error <= 0)
        {
            ++y;
            error += ty;
            ty += 2;
        }

        if (error > 0)
        {
            --x;
            tx += 2;
            error += (tx - diameter);
        }
    }
}

// Draw a ray to the screen given x,y,l,a
void DrawRay(SDL_Renderer *renderer, int32_t centreX, int32_t centreY, int32_t length, double angle)
{
    double dx = cosf(angle);
    double dy = sinf(angle);
    int out_x = dx * (double)length;
    int out_y = dy * (double)length;

    SDL_RenderDrawLine(renderer, centreX, centreY, centreX + out_x, centreY + out_y);
}

// Draw a point to the screen given x,y,l,a
void DrawPoint(SDL_Renderer *renderer, int32_t centreX, int32_t centreY, int32_t length, double angle)
{
    double dx = cosf(angle);
    double dy = sinf(angle);
    int out_x = dx * (double)length;
    int out_y = dy * (double)length;

    DrawCircle(renderer, centreX + out_x, centreY + out_y, 3);
}

// Returns a random number in the given range
double rand_in_range(double bottom, double top)
{
    double ret_val = ((double)rand() / (double)RAND_MAX) * (top - bottom) + bottom;
    if (ret_val > top || ret_val < bottom)
    {
        printf("%f t:%f b:%f\n", ret_val, top, bottom);
    }
    return ret_val;
}

// Compute the correct ray length given a set of collision objects (walls)
double get_ray_len(SDL_Rect (*walls)[], double x, double y, double angle)
{
    double dx = cosf(angle);
    double dy = sinf(angle);
    // Using int max here because double max overflows later when cast to int
    double length = INT_MAX;
    int i = 0;

    // Check every wall in the array
    while ((*walls)[i].x != -1)
    {
        double x_1 = (*walls)[i].x;
        double y_1 = (*walls)[i].y;
        double x_2 = (*walls)[i].w;
        double y_2 = (*walls)[i].h;

        // Calculates the determinant. If det = 0, the two lines are parallel
        // and will never collide.
        double det = dx * (y_2 - y_1) - dy * (x_2 - x_1);
        if (det != 0.0)
        {
            // Compute the length of the ray when it collides with the wall
            // (could be negative for rear-ward collisions)
            double ray_len = ((x_1 - x) * (y_2 - y_1) - (y_1 - y) * (x_2 - x_1)) / det;
            // Compute the length of the wall where the collision takes place.
            // Is between zero and 1 if the collision happens where the wall
            // exists.
            double wall_len = (dy * (x_1 - x) - dx * (y_1 - y)) / det;

            // Check that the collision is valid
            if (wall_len >= 0 && wall_len <= 1 && ray_len >= 0.0 && ray_len < length && ray_len >= 0)
            {
                length = ray_len;
            }
        }
        i++;
    }
    return length + rand_in_range(-length / 50, length / 50);
}

double safe_angle(double angle)
{
    if (angle < 0.0)
    {
        return angle + (abs(angle) / (2 * M_PI)) * 2 * M_PI;
    }
    else if (angle > 2 * M_PI)
    {
        return angle - (abs(angle) / (2 * M_PI)) * 2 * M_PI;
    }
    else
    {
        return angle;
    }
}

void drawRotatedRect(SDL_Renderer *renderer, int x, int y, int w, int h, double angle)
{
    double cosAngle = cosf(angle);
    double sinAngle = sinf(angle);

    SDL_Point points[5] = {
        {x - w, y + h},
        {x + w, y + h},
        {x + w, y - h},
        {x - w, y - h},
        {x - w, y + h}};

    for (int i = 0; i < 5; i++)
    {
        double dx = points[i].x - x;
        double dy = points[i].y - y;
        points[i].x = x + dx * cosAngle - dy * sinAngle;
        points[i].y = y + dx * sinAngle + dy * cosAngle;
    }

    SDL_RenderDrawLines(renderer, points, 5);
}

// Scale the input value between given output values, clamping if over/under
// max input.
double clamp_and_scale(double in_bottom, double in_top, double out_top, double input)
{
    double out_bottom = 0;
    double output;
    if (input >= in_top)
    {
        output = out_top;
    }
    else if (input <= out_bottom)
    {
        output = out_bottom;
    }
    else
    {
        input -= in_bottom;
        input /= in_top - in_bottom;
        input *= out_top - out_bottom;
        input += out_bottom;
        output = input;
    }
    return output;
}
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

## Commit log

2023-02-17 Got initial prototype for depth processign working! Its just a bit slow
2023-02-21 Used callgrind and kcachegrind to optimize resample_particles function. Took ~15% off cycle time, bringing resample_particles from 80% -> 65%. Use this headway to increase particle count from 5000 ->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
    [main.c]
2023-02-23 Updates to the readme including tests on Raspberry pis
2023-03-02 Added graph optimization, iterative closest point, function plot, and made some adjustments to particle filter.
    [2.54 mm DUPONT MALE PIN HEADER, IO, 2X20, RPi4ModelB.SLDPRT, 2.54 mm DUPONT MALE PIN HEADER, IO, 2X40, RPi4ModelB.SLDPRT, 2.54 mm DUPONT MALE PIN HEADER, POE, 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]
2023-03-03 Updates to the test framework. Not yet functional.
2023-03-10 Finished cad for V1 Navie
    [Gigabit Ethernet Port, RPi4ModelB.SLDPRT, OV5647_B0033.SLDPRT, PCB, RPi4ModelB.SLDPRT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]
2023-03-10 Added pwm speed control
2023-03-14 Added control prototype for Navie
2023-03-15 Got encoders working, but am losing a lot of backwards ticks, especialy at high speed.
2024-04-01 Added motor encoder source
2024-04-01 Rewrote control code. Accounts for fwd and rev encoder skipping, uses pigpio for PWM control, implements trapezoidal velocity control, has functions for driving straight and turning.
    [main.c]
2024-04-29 Updates to control code, better encoder use
